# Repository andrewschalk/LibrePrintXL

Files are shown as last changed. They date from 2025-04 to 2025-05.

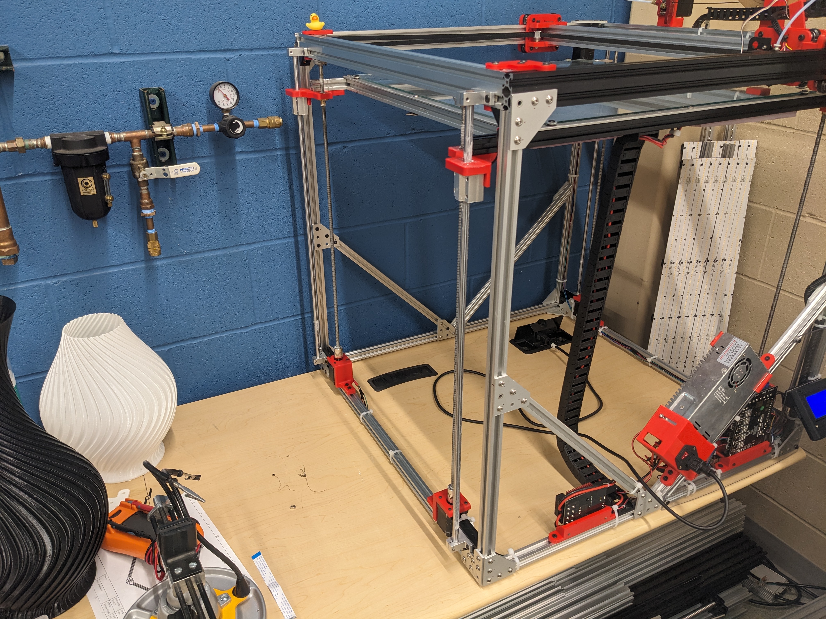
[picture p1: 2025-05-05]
Photos/Full_printer2.jpg

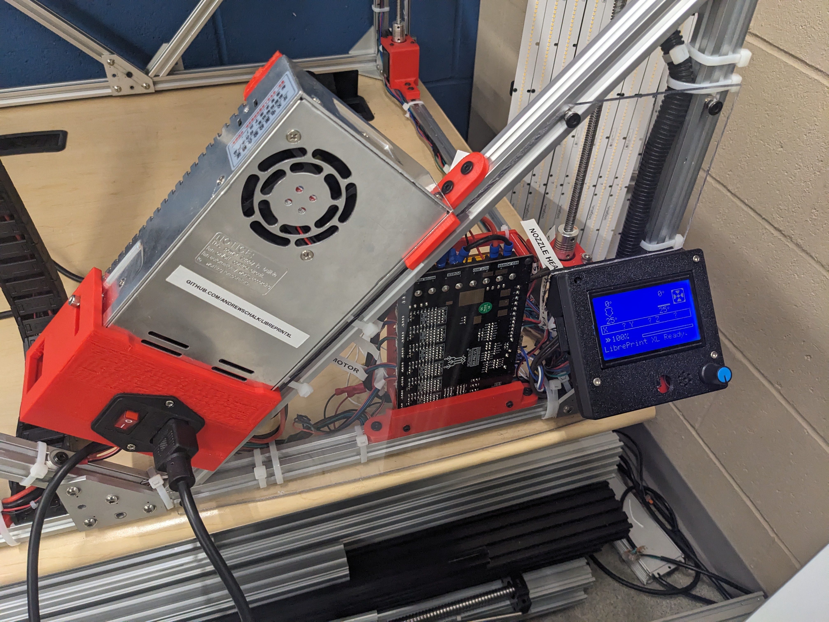
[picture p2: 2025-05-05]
Photos/Electronics_front2.jpg

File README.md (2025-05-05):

# LibrePrintXL
<p>

  </p>
A large open-source 3D printer.

See the [LibrePrint XL User Guide](/LibrePrint_XL_User_Guide.pdf) for steps on getting started.

See the v1.0.0 release on the right hand side for the full 3D model of the printer.







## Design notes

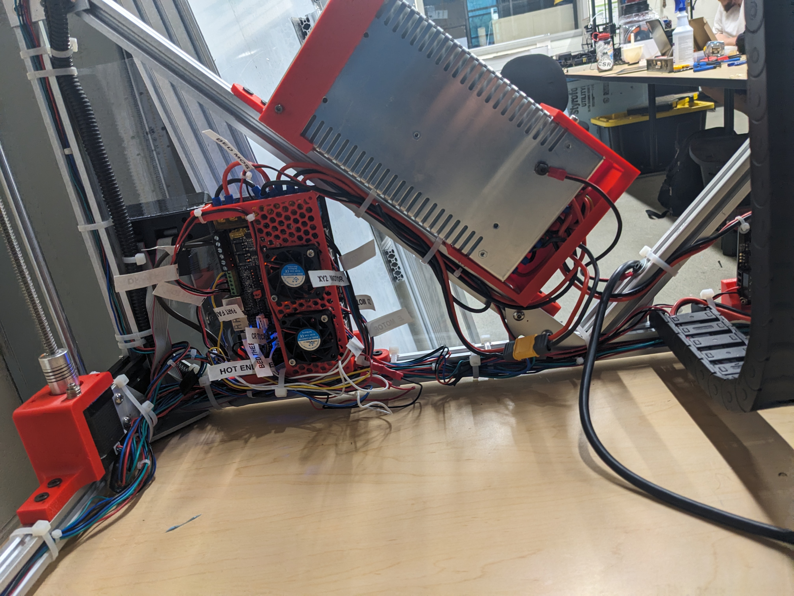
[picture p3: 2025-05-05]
Photos/Electronics_back.jpg

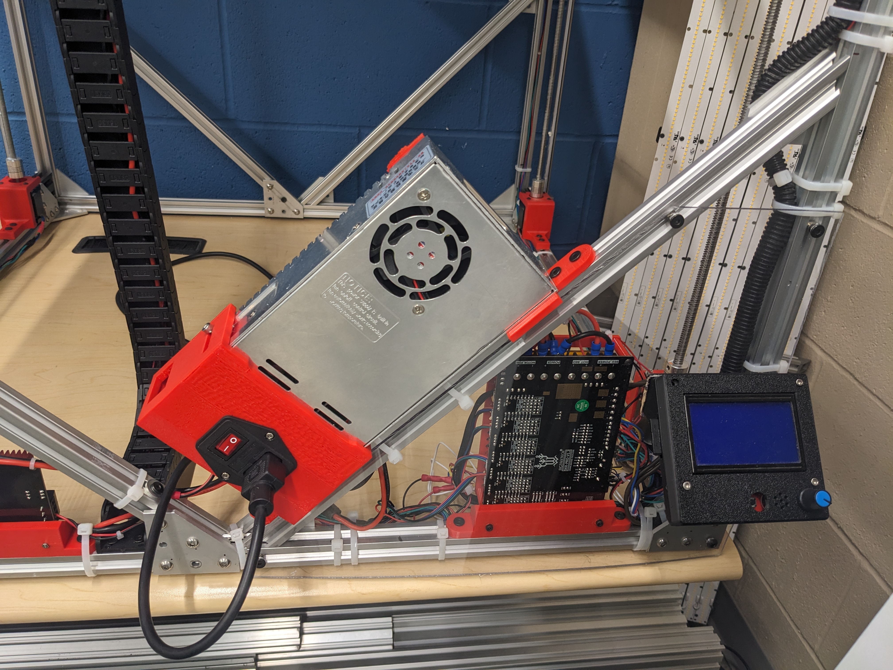
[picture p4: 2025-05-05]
Photos/Electronics_front.jpg

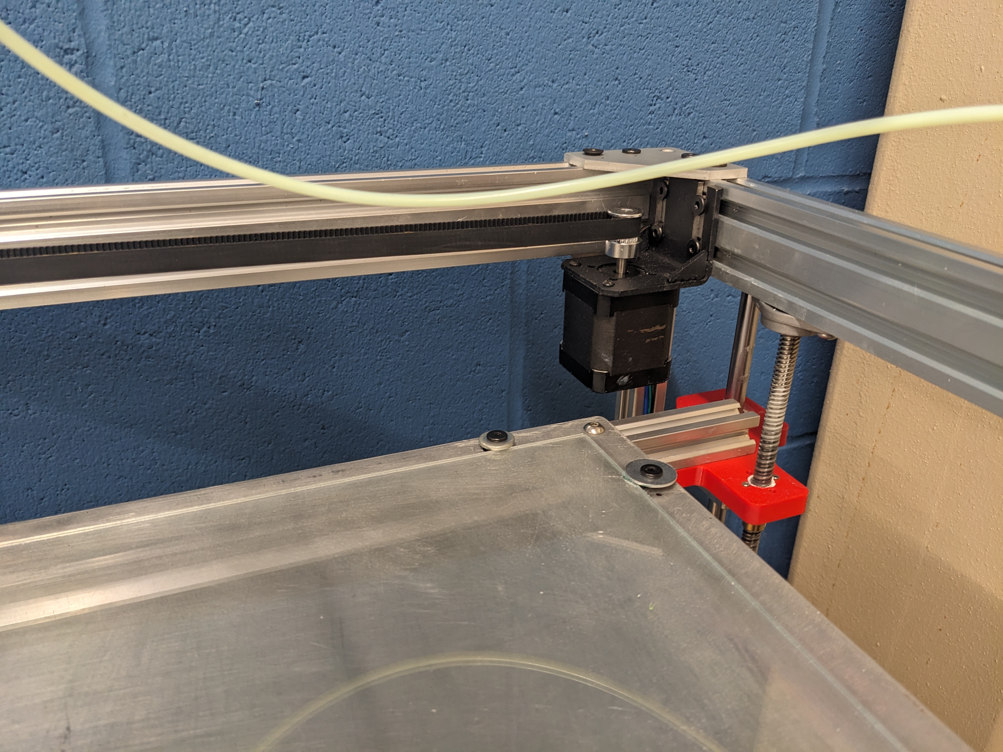
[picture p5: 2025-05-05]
Photos/CoreXY_Motor2.jpg

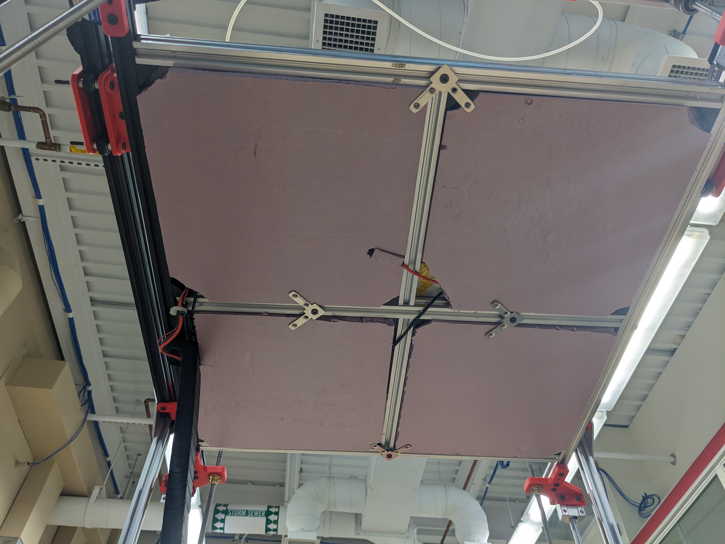
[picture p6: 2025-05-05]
Photos/Bed_underside.jpg

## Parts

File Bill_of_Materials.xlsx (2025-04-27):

Item | Part Number | Thumbnail | BOM Structure | Unit QTY | QTY | Stock Number | Description | REV
1 | HotBed |  | Normal | Each | 1
2 | 80-20610mm |  | Normal | Each | 2
3 | 80-20570mm |  | Normal | Each | 3
4 | 80-20275mm |  | Normal | Each | 2
5 | 4844N42_T-Slotted Framing Structural Bracket |  | Normal | Each | 10 |  | STEP AP203 | ANY
6 | HeatBed |  | Normal | Each | 4
11 | BLTouch-Smart V3.1 |  | Normal | Each | 0
13 | QSM-M5-4 |  | Normal | Each | 1 |  | SolidWorks IGES file using analytic representation for surfaces
15 | NF-A4x20 |  | Normal | Each | 2 |  | STEP AP214
16 | GantryPlate |  | Normal | Each | 6
17 | GantryBearing |  | Normal | Each | 12
18 | UNI 5931 - M 5 x 50 |  | Purchased | Each | 20 |  | Cylinder Head Cap Screw
20 | AS 1112 - M5 Type 5 |  | Purchased | Each | 20 |  | ISO metric hexagon nuts, including thin nuts, slotted nuts and castle nuts
23 | BeltFastener |  | Normal | Each | 2
24 | UNI 5931 - M 5 x 8 |  | Purchased | Each | 222 |  | Cylinder Head Cap Screw
25 | .25inSpacer |  | Normal | Each | 32
26 | 5mmSpacer |  | Normal | Each | 14
27 | 6627T231_Stepper Motor |  | Normal | Each | 7 |  | STEP AP203 | ANY
28 | 80-20base1 |  | Normal | Each | 2
29 | 80-20base2 |  | Normal | Each | 2
30 | 80-20Upright |  | Normal | Each | 4
31 | topBar1x2 |  | Normal | Each | 2
32 | topBar1x22 |  | Normal | Each | 2
33 | TSlotCornerGusset |  | Normal | Each | 10
34 | TSlotCornerGussetModified |  | Normal | Each | 4
35 | LinearRodSupport8020 |  | Normal | Each | 4
36 | CornerBracket |  | Normal | Each | 8
37 | 1277N11_Corrosion-Resistant Timing Belt Pulley |  | Normal | Each | 2 |  | STEP AP203 | ANY
38 | 1277N735_Corrosion-Resistant Timing Belt Pulley |  | Normal | Each | 8 |  | STEP AP203 | ANY
42 | 4516T501_Snap-Together Cable and Hose Carrier |  | Normal | Each | 34 |  | STEP AP203 | ANY
44 | SpoolHolder |  | Normal | Each | 0
45 | LinearRod |  | Normal | Each | 4
46 | Gantryconnect |  | Normal | Each | 4
47 | GantryBar |  | Normal | Each | 1
48 | Leadscrew nut M8 step2 by prodes |  | Normal | Each | 4 |  | STEP AP214 | ANY
49 | SC10 SCS10UU Linear Rail Bearing |  | Normal | Each | 4
50 | RodToBedCoupler |  | Normal | Each | 2
51 | 2391N25_Fast-Travel Ultra-Precision Lead Screw |  | Normal | Each | 4 |  | STEP AP203 | ANY
52 | RodToBedCouplerMirror |  | Normal | Each | 2
53 | Zinc Alloy Pillow Block Flange Bearing KFL08 ID-8mm |  | Normal | Each | 4
54 | UNI 5931 - M 3 x 5 |  | Purchased | Each | 48 |  | Cylinder Head Cap Screw
55 | NEMA17BaseHolder |  | Normal | Each | 4
56 | SK10 |  | Normal | Each | 8
57 | AS 1421 - M5 x 12 Cup Point |  | Purchased | Each | 8 |  | ISO metric hexagon socket set screws
58 | nema17-mount |  | Normal | Each | 2 |  | FreeCAD Model
59 | CoreXYPullyBlock |  | Normal | Each | 4
60 | RepRapDiscount_Full Graphic Smart Controller |  | Normal | Each | 1
61 | FG_lcd_front_Panel |  | Normal | Each | 1
62 | FG_lcd_rear_cover |  | Normal | Each | 1
63 | FAN |  | Normal | Each | 1
64 | SKR-PRO-V1.2 |  | Normal | Each | 1
65 | SKR Mount |  | Normal | Each | 1
66 | UNI 5931 - M 5 x 20 |  | Purchased | Each | 4 |  | Cylinder Head Cap Screw
67 | TMC2209 |  | Normal | Each | 6 |  | FreeCAD Model
68 | Raspberry Pi 4 Model B |  | Normal | Each | 1
69 | Raspberry_Pi_4_Case |  | Normal | Each | 1 |  | STEP AP214 | ANY
70 | UNI 5931 - M 2.5 x 4 |  | Purchased | Each | 4 |  | Cylinder Head Cap Screw
71 | Power Supply Cover Assembly |  | Normal | Each | 1
74 | 4147N168_Set Screw Precision Flexible Shaft Couplings |  | Normal | Each | 4 |  | STEP AP203 | ANY
75 | 10mmSpacer |  | Normal | Each | 8
76 | makerbase mks hotbed mos v1.1 |  | Normal | Each | 1 |  | CATIA V5 STEP Exchange
77 | HOTBED-MOSHolder |  | Normal | Each | 1
80 | Part2 | *Varies* | Normal | Each | 2
81 | Part1 | *Varies* | Normal | Each | 2
82 | Idler Bearing |  | Normal | Each | 1
83 | MK8 Drive Gear |  | Normal | Each | 1
84 | MK8_Exruder_004(yay) |  | Normal | Each | 1
85 | Part3 |  | Normal | Each | 1
86 | extruder motor stand |  | Normal | Each | 1
87 | FrameCrossBrace |  | Normal | Each | 4
88 | 45CornerGusset |  | Normal | Each | 8
89 | HOTEND ENDER 3 PRO |  | Normal | Each | 1
90 | DUTO DE AR BLOWER FAN DC PB04020MS4 |  | Normal | Each | 1
91 | BLOWER FAN DC PB04020MS4 |  | Normal | Each | 1
92 | Vis BHC 18mm |  | Normal | Each | 3
93 | CableCarrierMount |  | Normal | Each | 1
94 | UNI 5931 - M 5 x 25 |  | Purchased | Each | 1 |  | Cylinder Head Cap Screw

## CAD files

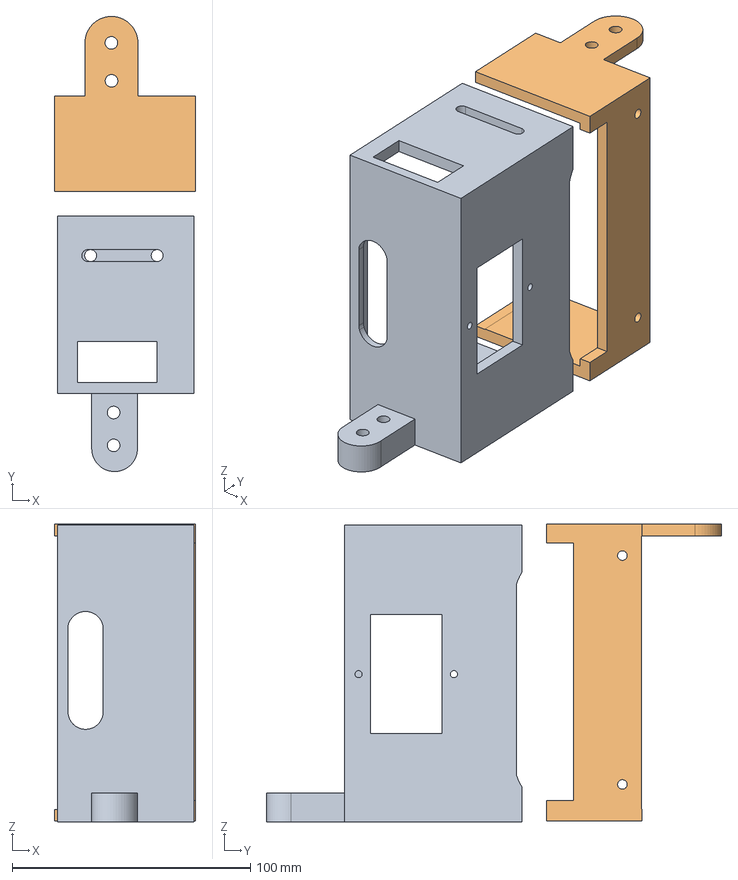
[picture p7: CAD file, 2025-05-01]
3D_Models/Power-supply-connector.stp
59.3 x 191.0 x 125.0 mm

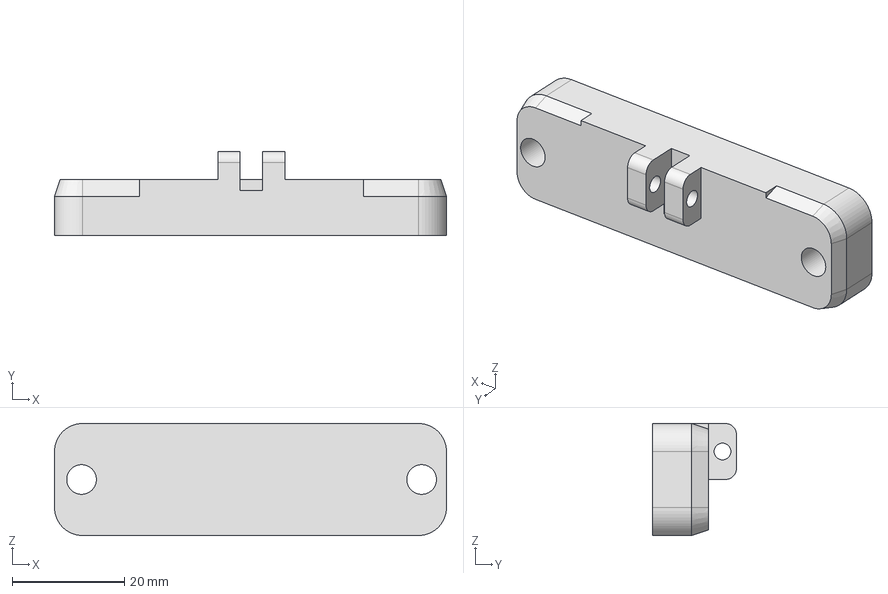
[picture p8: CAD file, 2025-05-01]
3D_Models/cameramountbottom.stp
70.0 x 15.0 x 20.0 mm

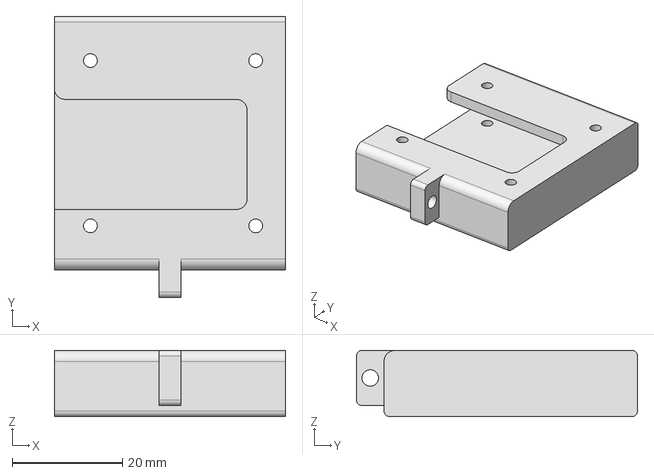
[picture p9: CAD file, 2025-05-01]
3D_Models/cameramounttop.stp
42.0 x 51.0 x 12.0 mm

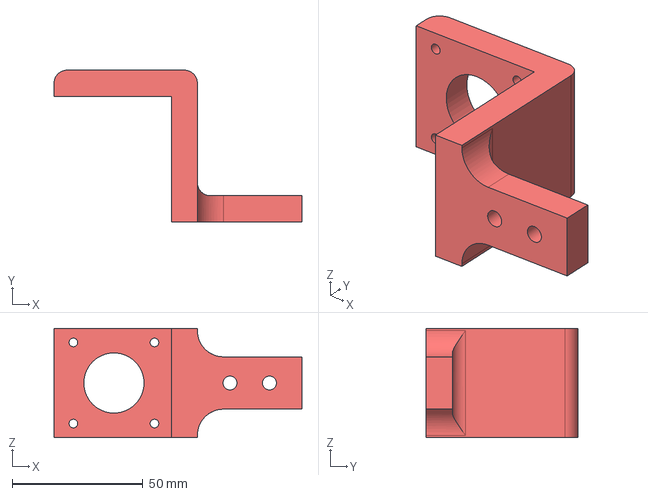
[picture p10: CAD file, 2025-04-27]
3D_Models/NEMA17BaseHolder.stp
94.8 x 58.0 x 41.8 mm

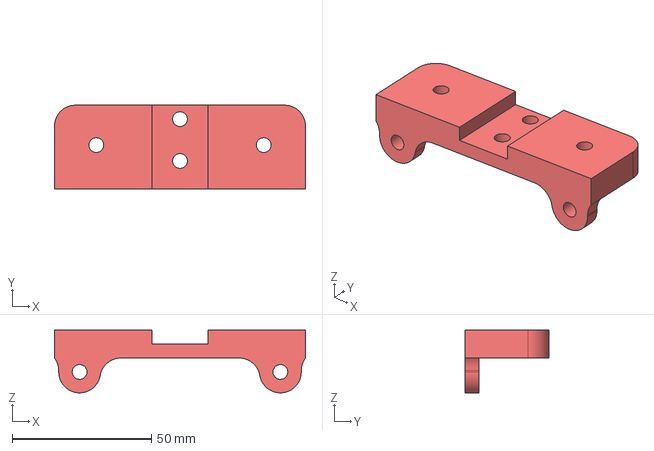
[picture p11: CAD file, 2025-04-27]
3D_Models/Gantryconnect.stp
90.0 x 30.0 x 22.5 mm

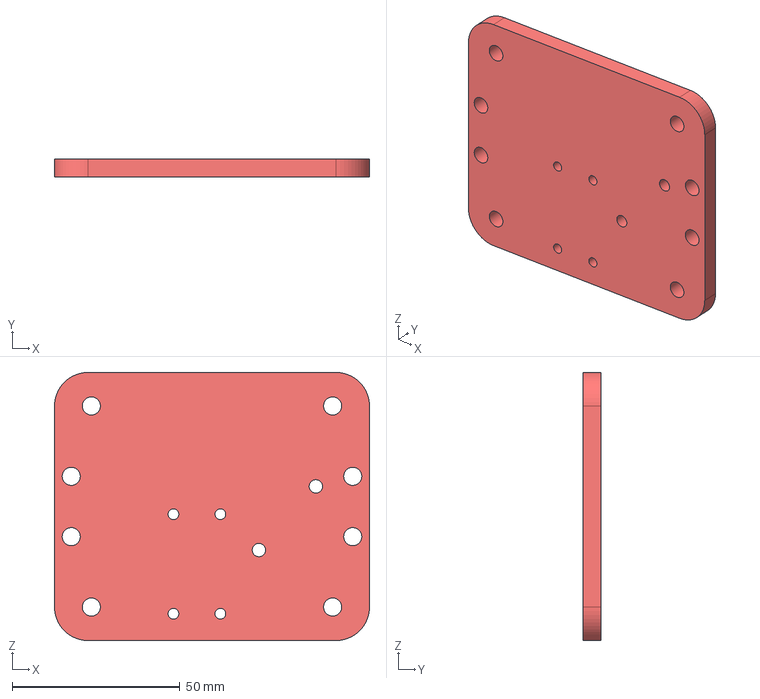
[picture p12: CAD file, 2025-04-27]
3D_Models/GantryPlate.stp
94.0 x 5.50 x 80.0 mm

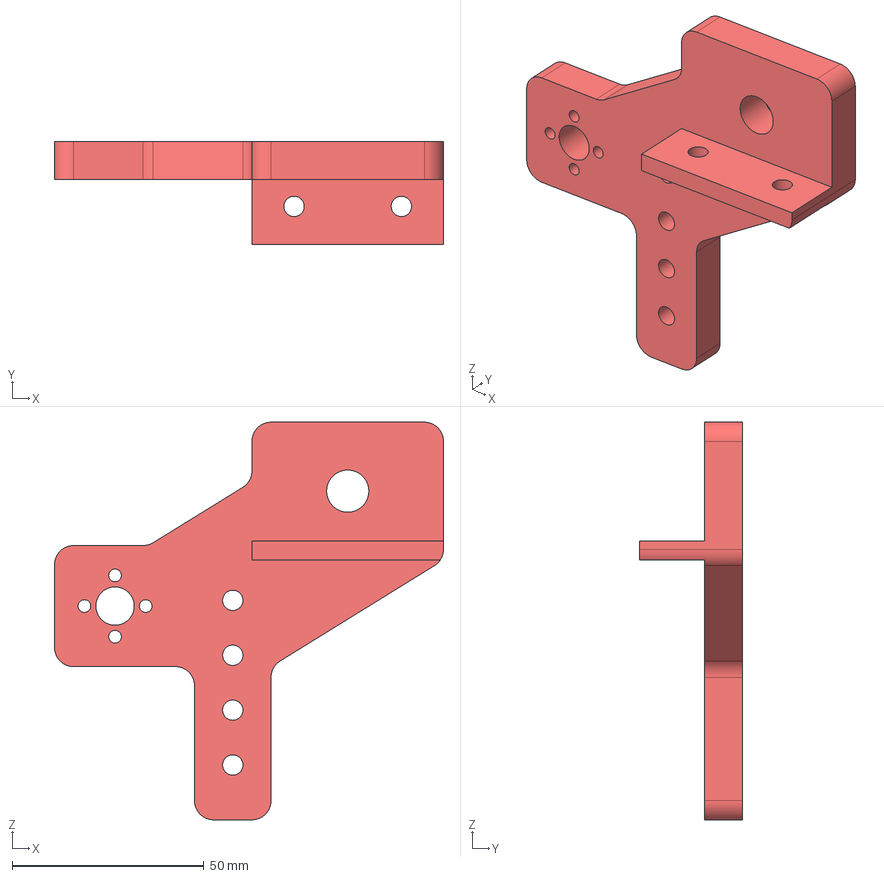
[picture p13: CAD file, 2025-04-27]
3D_Models/RodToBedCoupler.stp
101.5 x 27.0 x 103.8 mm

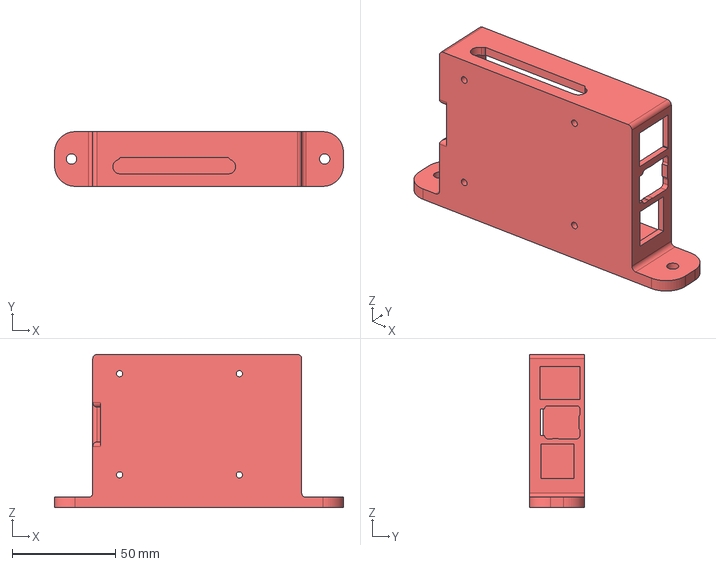
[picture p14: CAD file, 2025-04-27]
3D_Models/Raspberry_Pi_4_Case.stp
140.0 x 26.5 x 74.1 mm

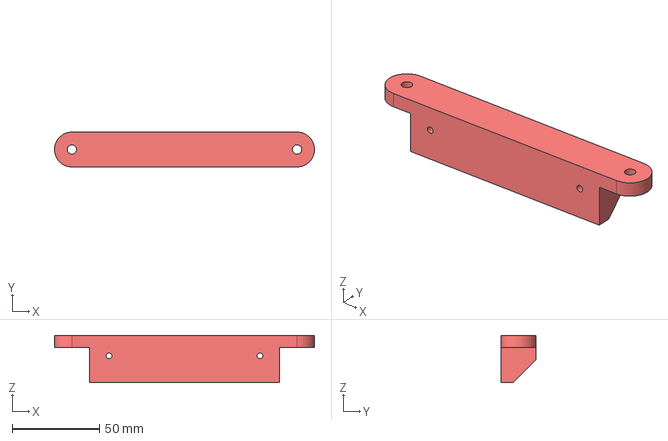
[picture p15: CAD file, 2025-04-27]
3D_Models/SKR Mount.stp
149.0 x 20.0 x 27.0 mm

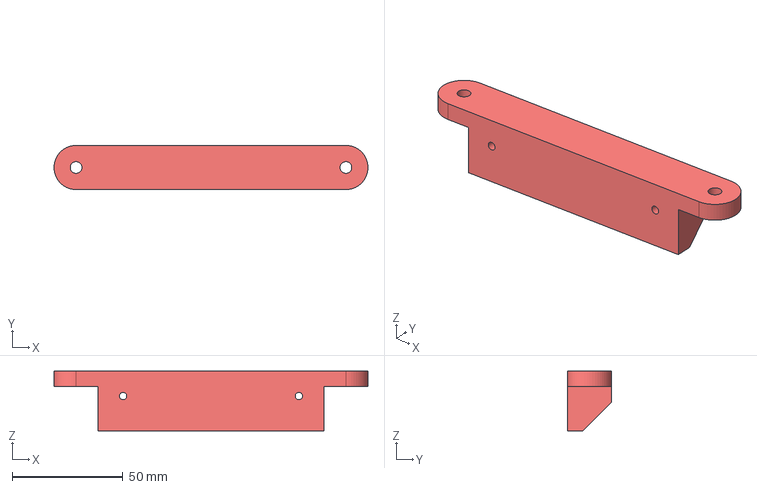
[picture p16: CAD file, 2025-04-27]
3D_Models/HOTBED-MOSHolder.stp
142.0 x 20.0 x 27.0 mm

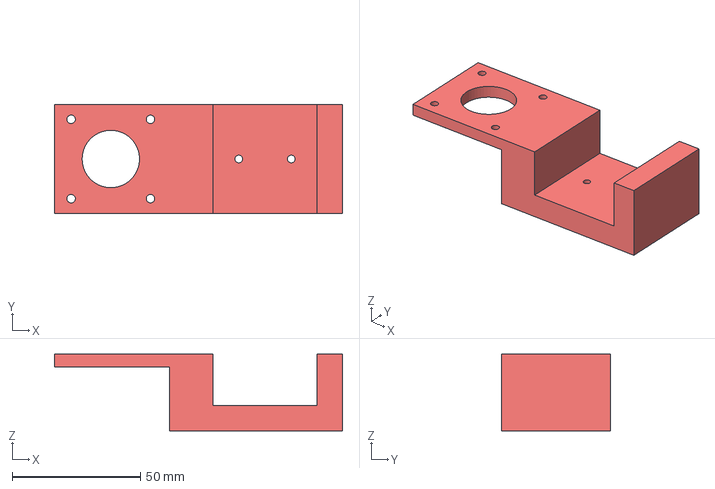
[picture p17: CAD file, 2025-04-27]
3D_Models/extruder motor stand.stp
112.5 x 42.5 x 30.0 mm

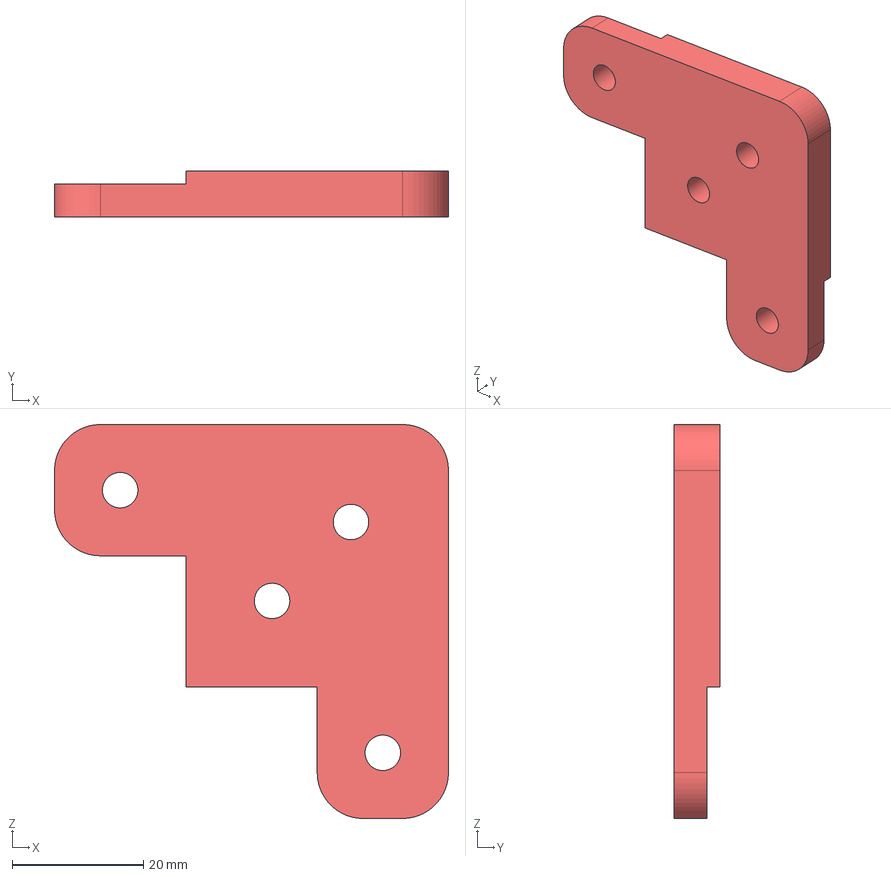
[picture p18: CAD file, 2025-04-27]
3D_Models/CoreXYPullyBlock.stp
60.0 x 7.00 x 60.0 mm

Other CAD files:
3D_Models/FG_lcd_front_Panel.stp
3D_Models/RodToBedCouplerMirror.stp
3D_Models/FG_lcd_rear_cover.stp
3D_Models/FANCover.stp

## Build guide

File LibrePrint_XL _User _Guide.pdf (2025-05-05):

# LibrePrint XL

## User Guide and Manual

## Created by

## Andrew Schalk

## Liam McGuire

## Reno Hoffman

## Christobol Alvarado

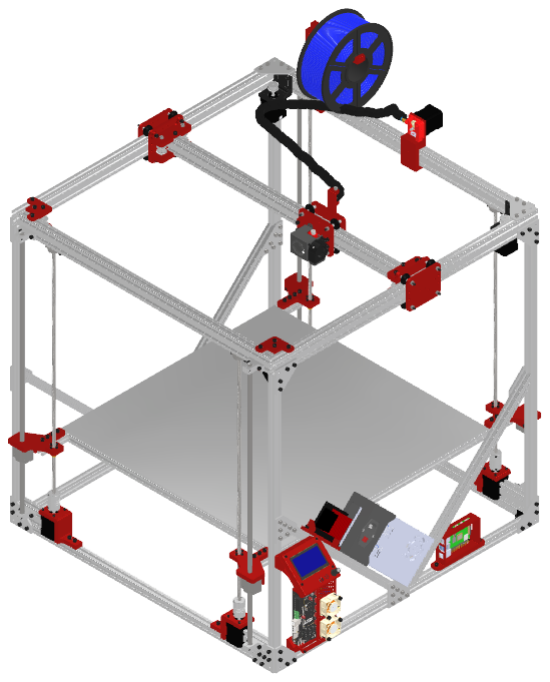
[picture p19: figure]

## Contents

## Printing a Part

Setting up PrusaSlicer

- Download and install the latest version of PrusaSlicer. (https://www.prusa3d.com/page/prusaslicer_424/) At the time of writing, this is
2.9.2. Any 2.X.X version of PrusaSlicer will be compatible with LibrePrint XL.
- Download “PrusaSlicer_LibrePrintXL.ini” from the Github (https://github.com/andrewschalk/LibrePrintXL). Be warned that using other profiles can lead to failed prints and even printer damage.
- Navigate to File -> Import -> Import Config Bundle. In the file browser that opens, select the profile you downloaded from Github.
- LibrePrint XL’s profiles are now loaded and you are ready to slice a model!

Slicing a Model

- The usage of PrusaSlicer is documented extensively on their website. (https://help.prusa3d.com/article/general-info_1910)
- Ensure that the proper profiles are selected
- Under “Print Settings” select “LibrePrintXL”
- Under “Filaments” select “LibrePrintXL_PLA”
- Under “Printers” select “LibrePrintXL”
- No modifications to these profiles are needed
- Add a model to the print space, slice the model, and export the Gcode to an SD card.

Mechanical Calibration

- Visually inspect the bed, if it looks to be out of level by greater than 2° in any direction, manual leveling must be performed (see “manual bed leveling). Software bed leveling will account for small errors in bed levelness, but large errors can cause mechanical failure.
- Make sure that the printer has enough room for moving parts to not contact surrounding objects. Ensure that:
- All four corners of the bed can move up and down
- The wire carrier which holds the wires for the print head can protrude horizontally above the user interface
- The y-gantry on both sides can move forwards and backwards.

- The space beneath the printer is clear

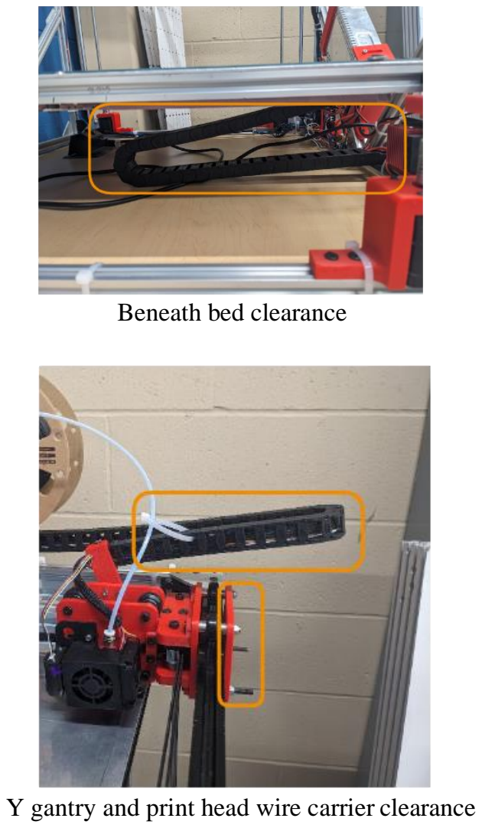
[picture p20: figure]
Beneath bed clearance

Y gantry and print head wire carrier clearance

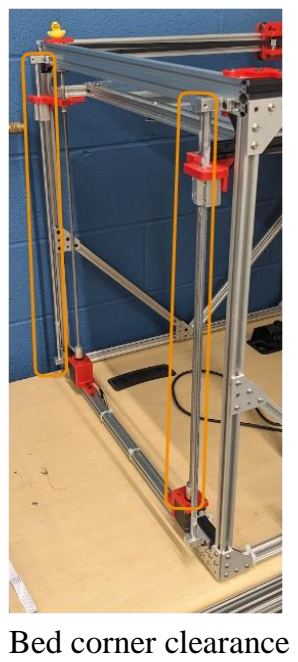
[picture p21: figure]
Bed corner clearance

Printing a File

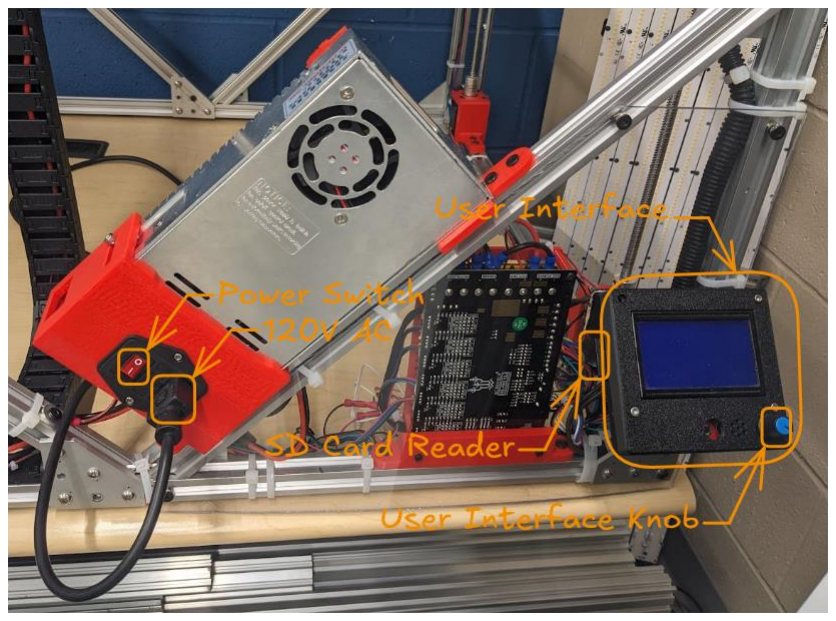
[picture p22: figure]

- See “Unloading Filament” and “Loading Filament” if filament needs to be replaced
- Put the SD card in the slot on the left side of the user interface.
- Turn on the printer with the power switch
- Wait for the info screen to appear
- Press the knob on the user interface to enter the menu. Turning the knob will navigate through the menu
- Select Print from Media -> YourFileName.gcode -> Print
- The info screen will appear saying “Bed Heating…” at the bottom, indicating that the print is starting.
- The bed and hot end will heat up, all three axes will move to home, and the print head will probe the bed. Once this is complete, the printing will begin.
- Verify that the first layer is printed properly and allow the print to complete
- The screen will indicate the percentage completed and how long the print has been running.

Unloading Filament (For PLA)

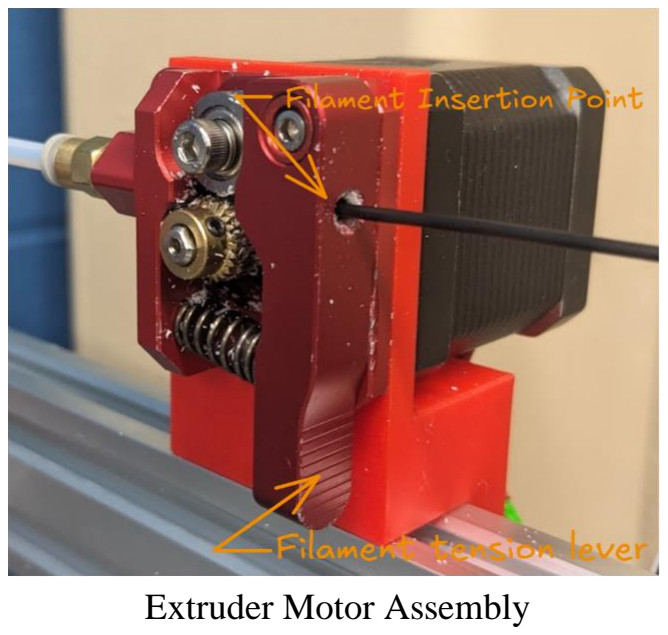
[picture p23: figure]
Extruder Motor Assembly

- Heat up the extruder nozzle to 260°C using the user interface.
- Press the user knob to navigate to the main menu.
- Select Temperature -> Nozzle
- Turn the knob until the number reads 260°C
- Press the knob. The nozzle will begin to heat up and you will be taken back to the temperature page.
- Select Main -> Info Screen to monitor the temperature
- Once the nozzle has reached 260°C, you may begin unloading filament
- Press and hold the filament tension lever to free the filament
- Pull the filament gently until it comes completely out of the printer
- If the filament is hard to pull, first push the filament farther into the extruder to melt built up plastic off of the end and then pull

Loading Filament (For PLA)

- From the “Unloading Filament” section, the nozzle should already be heated to 260°C. If not, the following steps describe the heating process
- Press the user knob to navigate to the main menu.
- Select Temperature -> Nozzle
- Turn the knob until the number reads 260°C
- Press the knob. The nozzle will begin to heat up and you will be taken back to the temperature page.
- Select Main -> Info Screen to monitor the temperature
- Once the nozzle has reached 260°C, you may begin loading filament.

- Cut off any ragged bits at the end of the filament and straighten out the last 2 inches by hand
- Press and hold the filament tension lever
- Insert the filament into the filament insertion point and push the filament until it begins to extrude out of the nozzle
- Wait until the old color has been purged, the filament has been successfully loaded and you are ready to print
- Remove any stray plastic that may have been extruded during filament loading

## Troubleshooting

LibrePrint XL is based on standard 3D printer design methods so the solutions to any issues not listed here can usually be found online.

First layer issues

- The nozzle is too close or too far from the bed
- During a print, the z-offset may be set by menu -> tune -> Z babystepping
- While the first layer is being laid by the printer, turn the knob to slowly move the nozzle away or towards the bed

CoreXY belt loose

- If the belt comes loose, pull belt taught and tighten screws on the extruder mount holding belt in place. The belt should be tight enough to be easy to move and vibrate like a guitar string when plucked but not loose enough to sag.
- Command the X axis and Y axis to move using the touch screen, observe their movements to ensure they move properly. Info Screen -> Main Screen -> Move Axis -> Move X -> 1mm.
- Move in the X-axis several times to ensure it moves correctly
- Repeat the process for the Y-Axis
- Info Screen -> Main Screen -> Move Axis -> Move Y -> 1mm.

Thermal Runaway

- The screen displays “THERMAL RUNAWAY PRINTER HALTED Please reset”
- This is the printer recognizing an issue with the commanded heating and the sensed temperature.
- Test the operation of the heating functions !!While it is not likely, it is possible that these systems could heat to a dangerous level if broken, keep an eye on the heat while troubleshooting
- Heat the nozzle to 260°C

- Heat the bed to 60°C
- If both systems work well, the system is likely fine, this error may have been a false positive. If the error occurs again, check the thermal sensor and heating element for loose wiring.
- If one system fails, note the actual temperature and displayed temperature
- If the system begins to heat but the temperature doesn’t change, consider rewiring or replacing the temperature sensor
- If the system does not heat, consider rewiring or replacing the heating element

Filament Slipping

- If there is an issue with any part of the extruder assembly, it may cause the filament to slip preventing it from printing properly
- Brass pinion gear on extruder motor shaft may not be contacting filament
- If the brass pinion gear is not contacting the filament unscrew the set screw in the pinion, move the pinionup towards the filament and then tighten it back on
- To test extrusion, begin by heating the extruder to 260°C this can be done by menu ->temperature -> nozzle
- Once the nozzle is heated up, feed the filament into the extruder.
- Menu -> Motion -> Move Axis -> Move Extruder -> Move 1mm.
- Rotate the user knob until the filament extrudes from the nozzle.
- Observe extruder motor and ensure gear is moving filament.

Under Extrusion

- Ensure that the filament roll is oriented on the stand such that the plastic is being fed into the extruder at the same height.
- Measure on the filament role from the entrance of the extruder motor to a pre-determined distance. 10-20mm should be sufficient. Mark the filament that distance
- Rotate the user knob that distance. The mark should reach the entrance of the extruder motor and stop.

Hot-End Loose

- !! This may be a symptom of other issues. If the hot end fan is not working, the hot end fasteners may get too hot causing the hot end to sag in the plastic.
- The hot end fan will turn on if the hot end is above 60°C.
- Verify that the fan turns on by setting the hot end temperature to 260°C and waiting for the fan to turn on. menu -> temperature -> nozzle
- This may be fixed by retightening the two bolts that hold the hot end to its mount. These are held tight with lock washers so there should be no need for thread locker. If they keep coming loose, add thread locker.
- The two screws may be reached by putting through

Z-axis Squeaking or Binding

- Review procedure for manual bed leveling
- Review procedure for lubricating z-axis
- Verify all z-axis fasteners are tight by attempting to wiggle the parts they fasten

Loose Parts/Fasteners

The fasteners are all held in place by either thread locker or nylon lock nuts. When tightening fasteners, be considerate of the materials being held together and the force used. Plastic and even aluminum can deform from tightening too much.

- If a nylon lock nut becomes loose, it may be sufficient to tighten it back into place. If it does not stay in place, replace the lock nut with a new one.
- If there is not a nylon lock nut, the fastener is held in place with thread locker. The fastener must be removed and thread locker(locktite blue is good, do not use red) applied before retightening.

Broken Part

- Any part may be found in the bill of materials for replacement
- 3D printed part files are in the LibrePrint XL GitHub
- When replacing fasteners, they need to be properly secured again. If this is not done, the part may become loose, causing print failures or printer damage.
- Fasteners with nylon lock nuts should have the lock nut replaced, lock nuts lose some of their locking force after being used once.
- Fasteners without nylon lock nuts should have thread locker (locktite blue is good, do not use red) applied before securing.

Stringy and Saggy print(or other print quality issues)

This can be caused by many issues so it may be best to search up the specific issue online. This kind of error can usually be fixed by tuning slicer settings.

- Different brands of filament may need different settings even if they’re the same type of plastic.
- The temperature that we found worked best for the overture brand filament was 260°C. Another (no-name brand) was found to work best around 220°C and 260°C was far too hot. Research a “temperature tower” to tune the temperature for your filament.

## Electrical Specifications

- The frame and bed are connected to earth through the power supply case.

Wiring Schematic

- Each wire is labeled with a white flag to identify what it is
- Example: “XY1” means that this is the XY1 motor
- Use the following schematic to find the ports that these devices plug into
- Wire pairs which consist of just a red and black wire will plug into the positive and negative pins respectively
- Most connectors can only be plugged in one way. The exception is the CR touch whose connection is described in the schematic

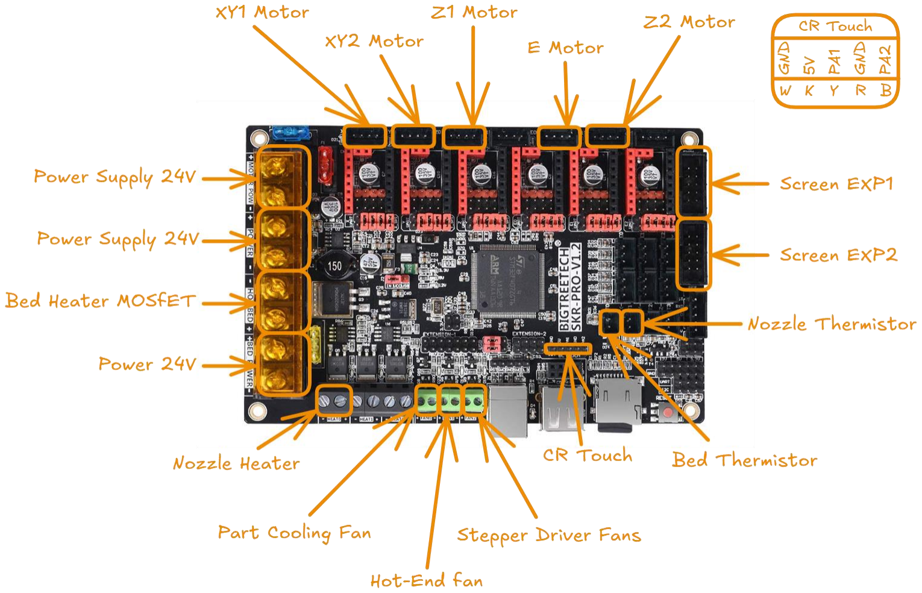
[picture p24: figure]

Bed Circuit Diagram

The 24V source is provided by the bed heater MOSFET

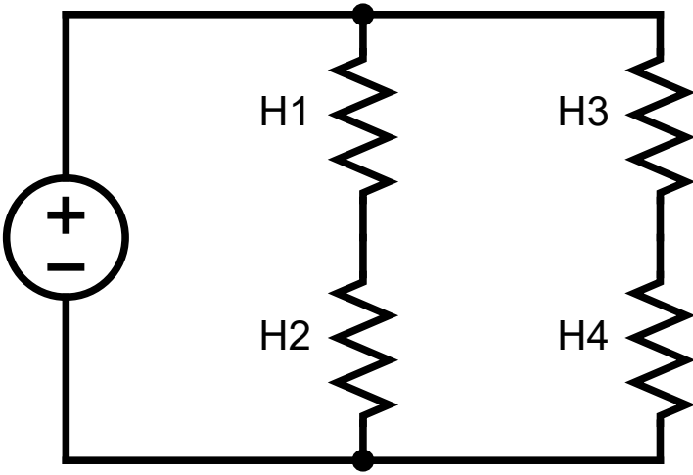
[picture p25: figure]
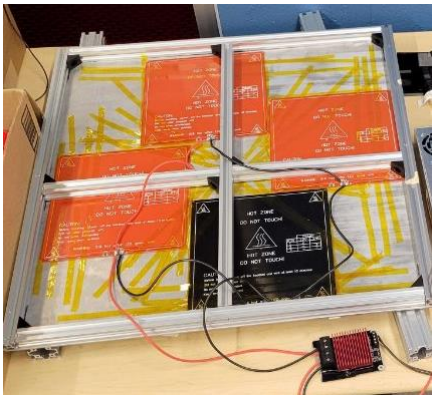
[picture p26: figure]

## Mechanical Specifications

CoreXY

## Firmware

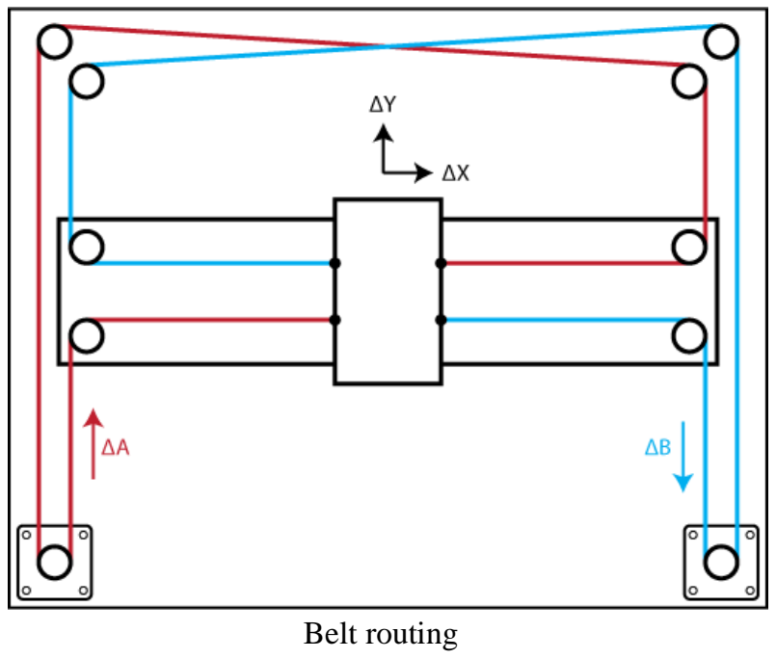
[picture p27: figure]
Belt routing

- LibrePrint XL uses a custom version of Marlin 2.1.2.5. Anything not discussed here can be referenced in the Marlin documentation. (https://marlinfw.org/)
- The files needed to rebuild LibrePrint XL’s firmware are on the GitHub. Marlin provides tutorials on how to develop and flash this firmware.

## Maintenance and Calibration

Manual Bed Leveling

This should be performed every 50 hours of printing or whenever the bed is out of level by greater than 2° in any direction. Software bed leveling will account for small errors in levelness, but large errors can cause mechanical failure.

- Needed
- A small, flat, object about ½ inch in one dimension. This will be used as a ground truth for the distance between the nozzle and points on the bed.

- Turn on the printer, press the user button, and select Motion -> Auto home. This will cause the printer to move to the home position
- Once homing is complete, from the motion menu, select Move Axis -> Move Z -> Move 1mm.
- Turn the knob clockwise to move the z-axis by 1mm increments until your flat object fits between the bed and the nozzle. This does not need to be precise
- Turn off the printer. (This disables the motors for the next step)
- Each corner of the bed will be brought to the same height by moving the nozzle to each corner and adjusting the position of the motor at that corner
- With your flat object between the nozzle and bed, rotate the coupling at the base of the z-axis lead screw to move the bed up until the nozzle just barely contacts the top of your flat object. The best way to do this is to move your flat object back and forth slowly on the bed while moving the bed up. You’ll know when the nozzle is touching when you feel a small amount of resistance to moving your flat object.

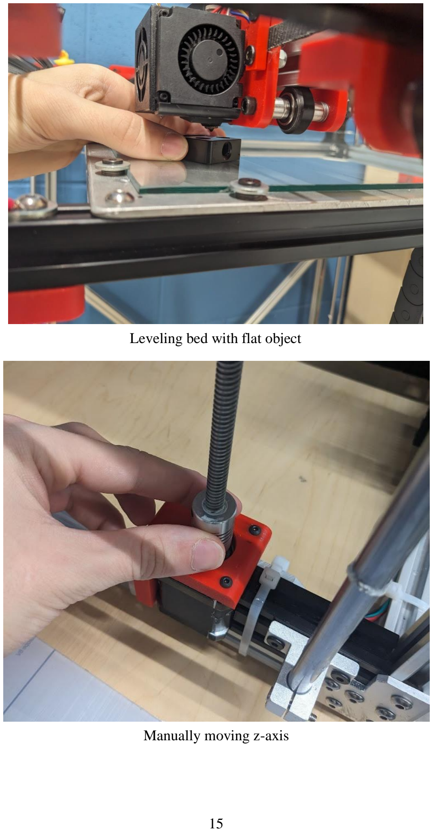
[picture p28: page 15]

Manually moving z-axis

Leveling bed with flat object

- By hand, slowly move the print head close to another corner on the bed and repeat the prior step for each corner. !! Moving too fast will generate a voltage which could damage the printer, if the screen lights up while the printer is off, you’re moving too fast.
- After all corners have been set to the same height, bed leveling is complete.

Lubricating Z-axis

This should be performed every 100 hours of printing or whenever the z-axis starts to squeak.

- Needed
- White lithium grease (Lucas Oil Products Inc. NLGI #2 is what we used)
- All four z-axis lead screws and all four z-axis linear rods should be greased
- Squeeze a thin layer of grease (about 1/16 of an inch thick) onto the lead screws and linear rods, all the way from the top to the bottom.
- Use nitrile gloves or a paper towel to spread the grease all around the linear rods. This does not need to be done on the lead screws, the lead screws will spread the grease when they rotate.
- Move the z-axis through its entire range of motion by pressing the knob and selecting Motion -> Move Axis -> Move Z -> Move 10mm. Turning the knob will move the bed in 10mm increments
- Wipe off any excess grease built up from movement

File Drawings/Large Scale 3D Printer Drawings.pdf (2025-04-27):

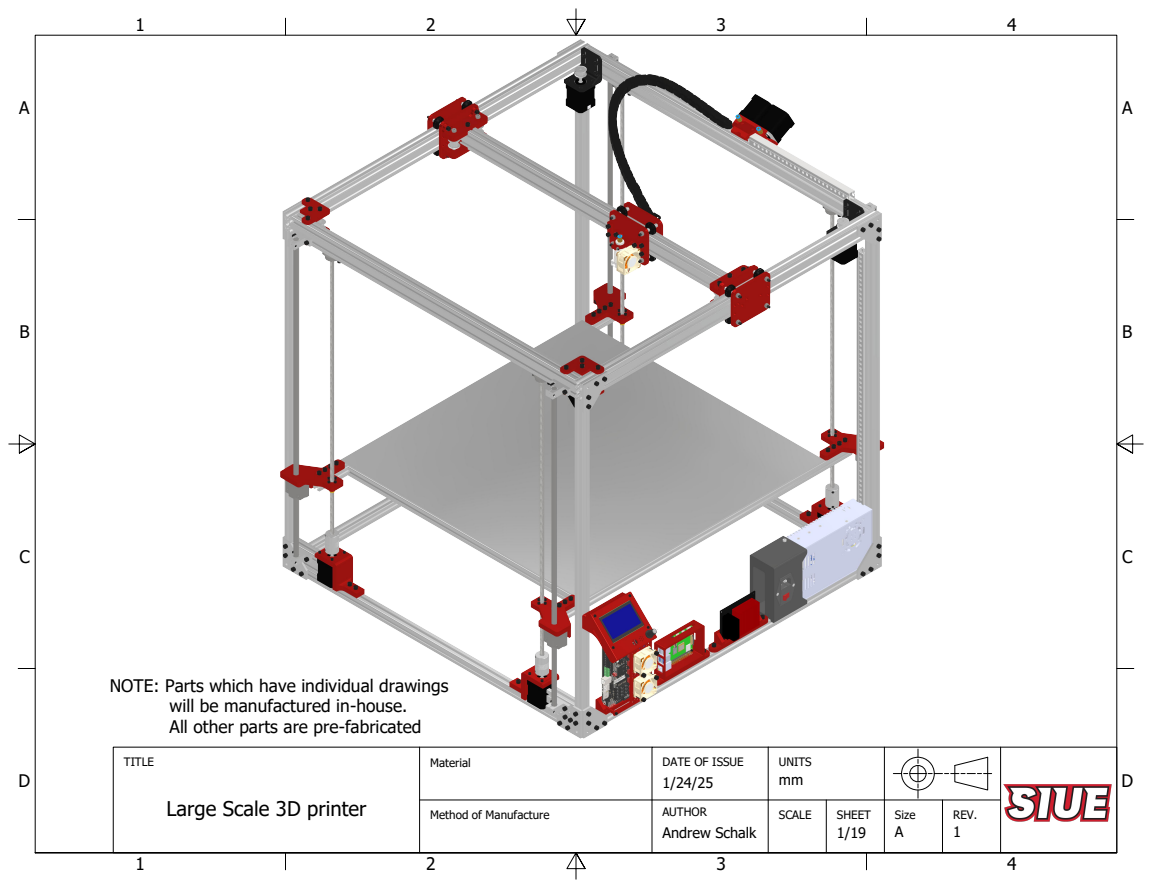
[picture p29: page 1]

NOTE: Parts which have individual drawings

will be manufactured in-house.
All other parts are pre-fabricated

TITLE Large Scale 3D printer | Material | DATE OF ISSUE 1/24/25 | UNITS mm

Method of Manufacture | AUTHOR Andrew Schalk | SCALE | SHEET | Size A | REV.

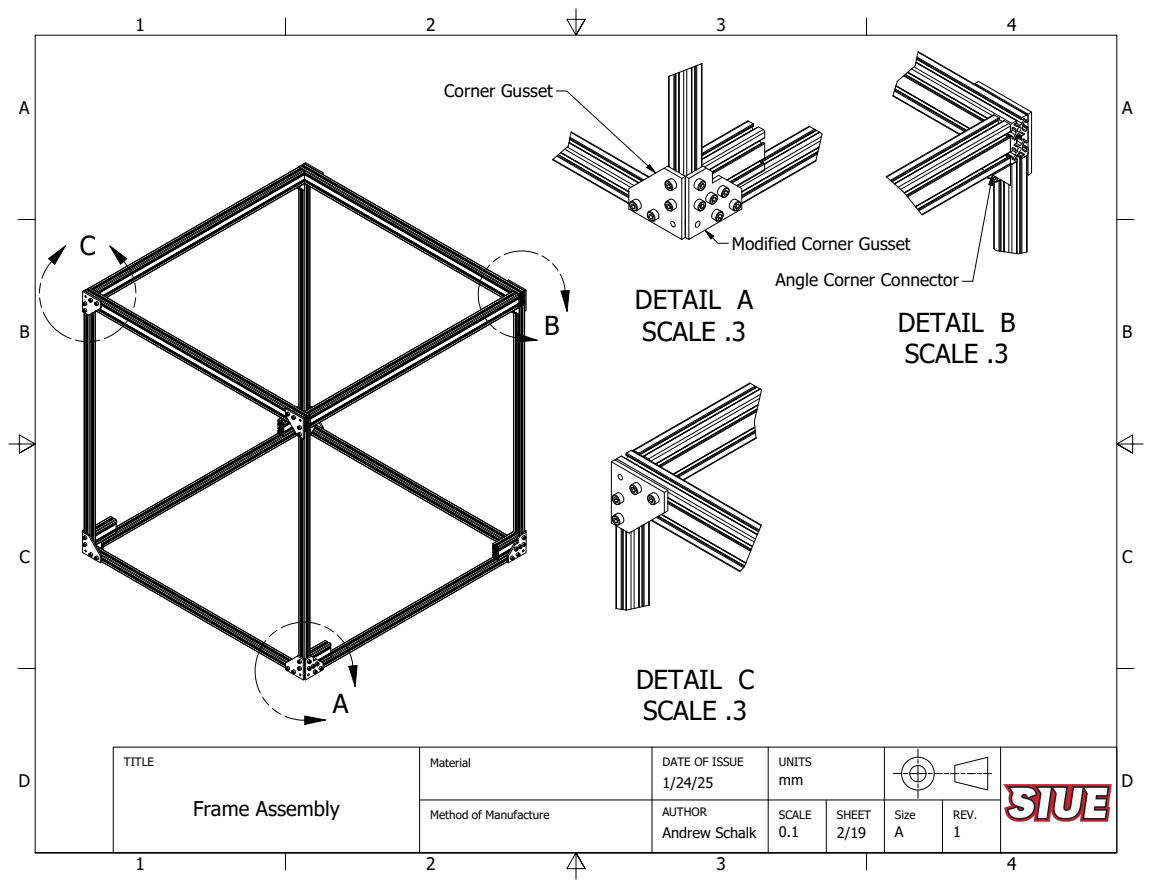
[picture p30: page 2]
DETAIL A; SCALE .3; DETAIL B; DETAIL C; Corner Gusset

Modified Corner Gusset

Angle Corner Connector

TITLE Frame Assembly | Material | DATE OF ISSUE 1/24/25 | UNITS mm

Method of Manufacture | AUTHOR | SCALE 0.1 | SHEET | Size | REV.

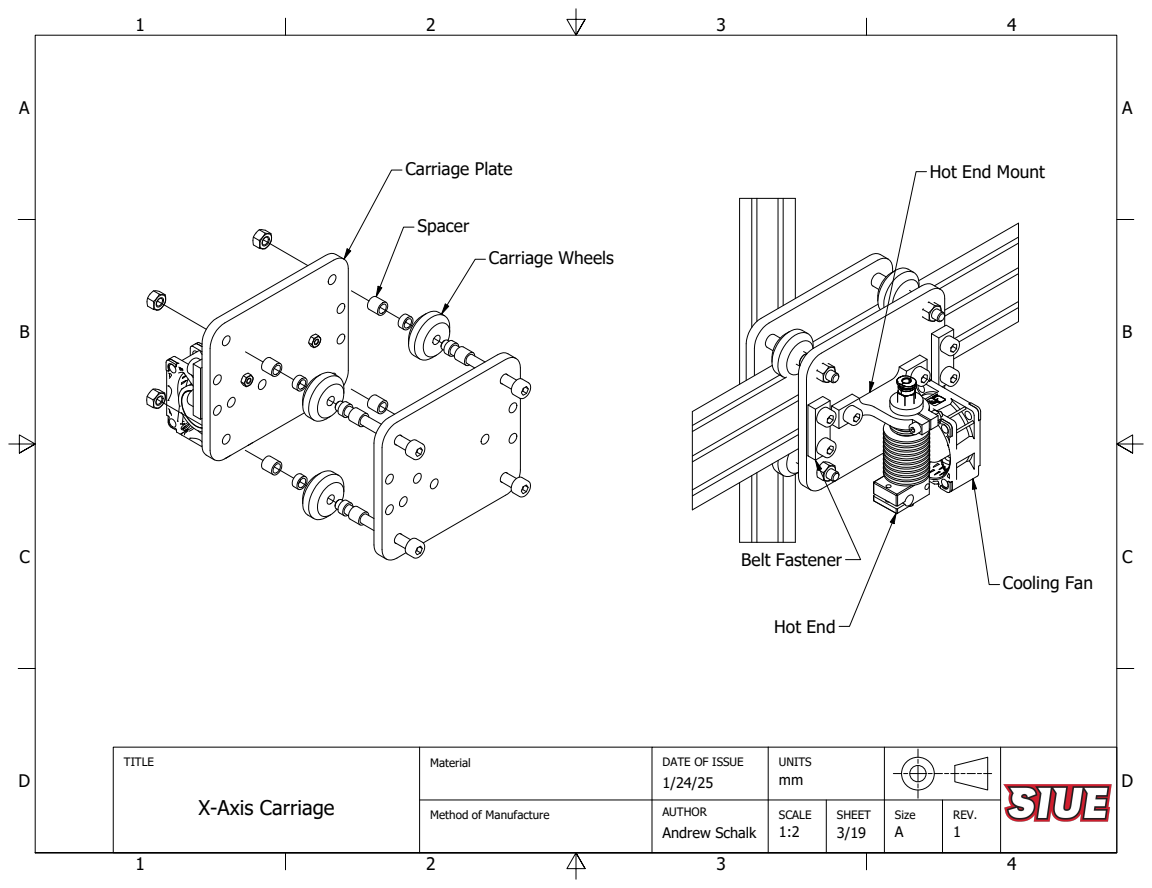
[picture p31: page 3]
Carriage Plate; Cooling Fan; Belt Fastener; Hot End; Carriage Wheels

Hot End Mount

TITLE X-Axis Carriage | Material | DATE OF ISSUE 1/24/25 | UNITS mm

Method of Manufacture | AUTHOR | SCALE 1:2 | SHEET | Size | REV.

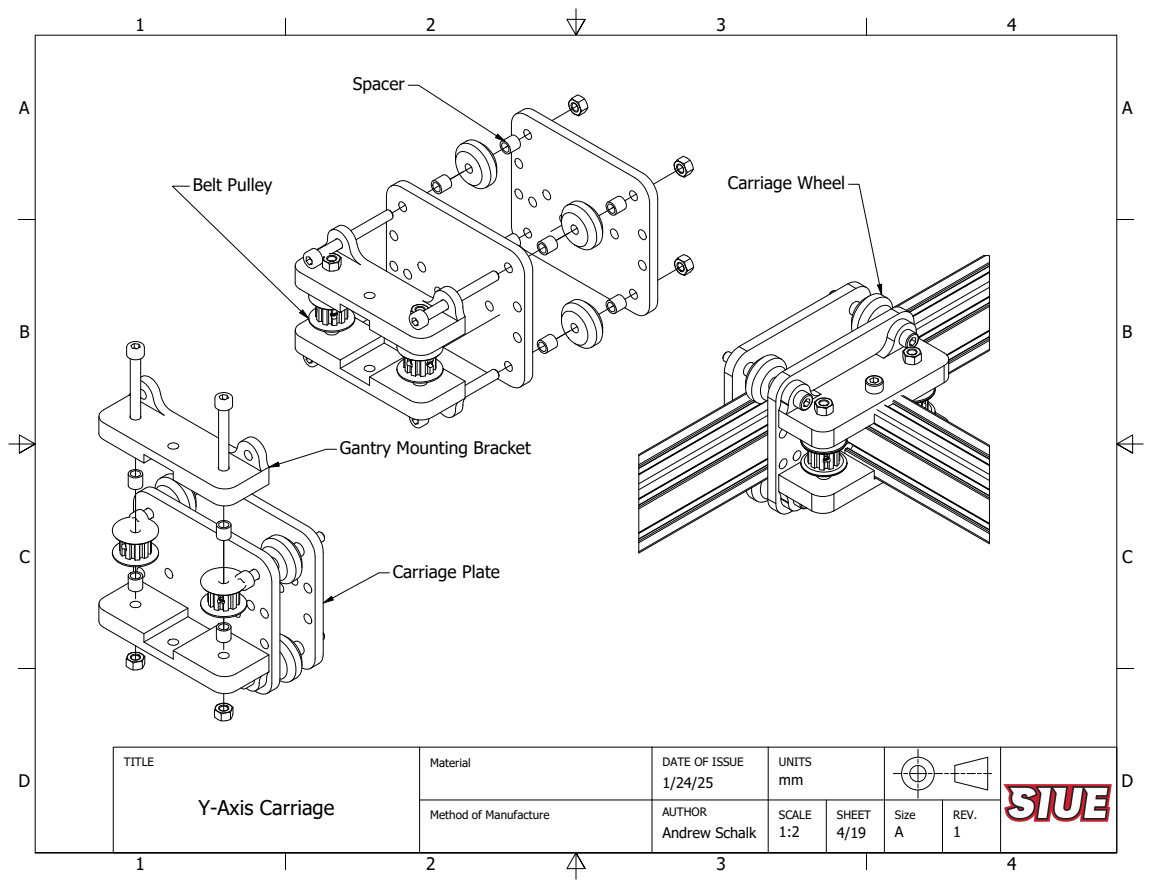
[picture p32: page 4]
Belt Pulley; Carriage Plate; Carriage Wheel

Gantry Mounting Bracket

TITLE Y-Axis Carriage | Material | DATE OF ISSUE 1/24/25 | UNITS mm

Method of Manufacture | AUTHOR | SCALE 1:2 | SHEET | Size | REV.

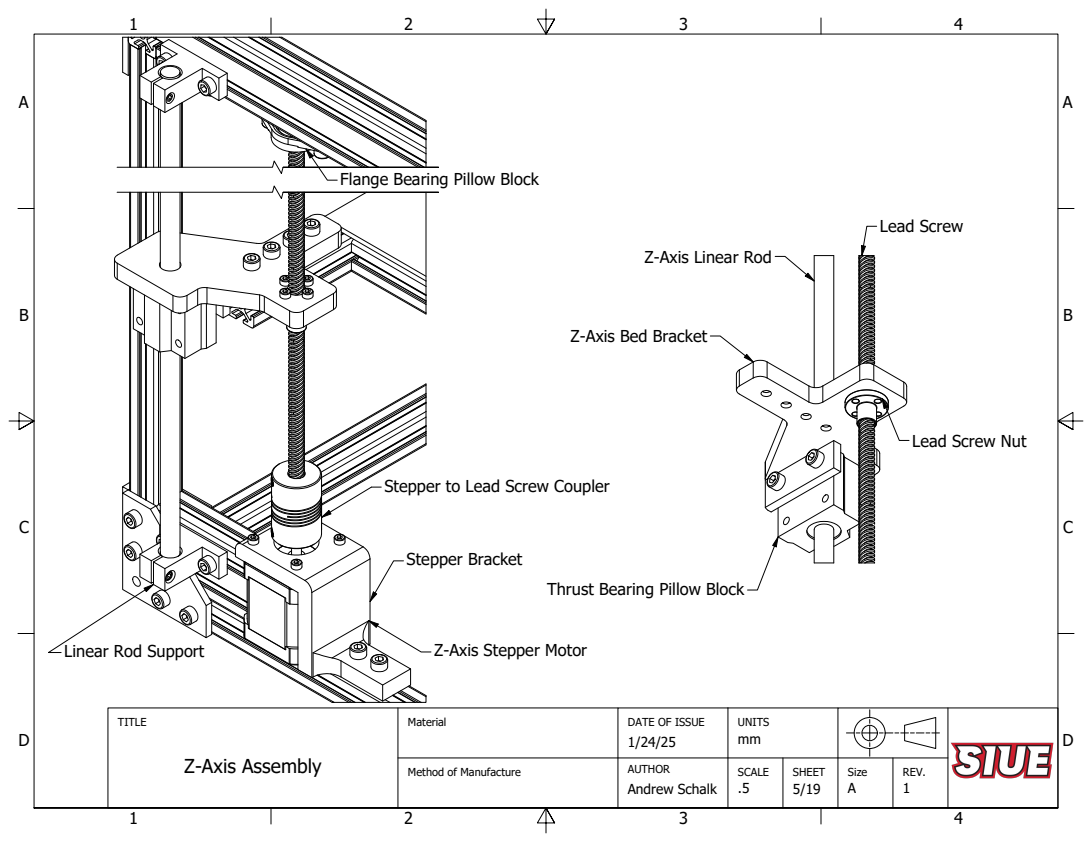
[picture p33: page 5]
Lead Screw; Stepper Bracket

Flange Bearing Pillow Block

Z-Axis Linear Rod

Z-Axis Bed Bracket

Lead Screw Nut

Stepper to Lead Screw Coupler

Thrust Bearing Pillow Block

Linear Rod Support

Z-Axis Stepper Motor

TITLE Z-Axis Assembly | Material | DATE OF ISSUE 1/24/25 | UNITS mm

Method of Manufacture | AUTHOR | SCALE | SHEET | Size | REV.

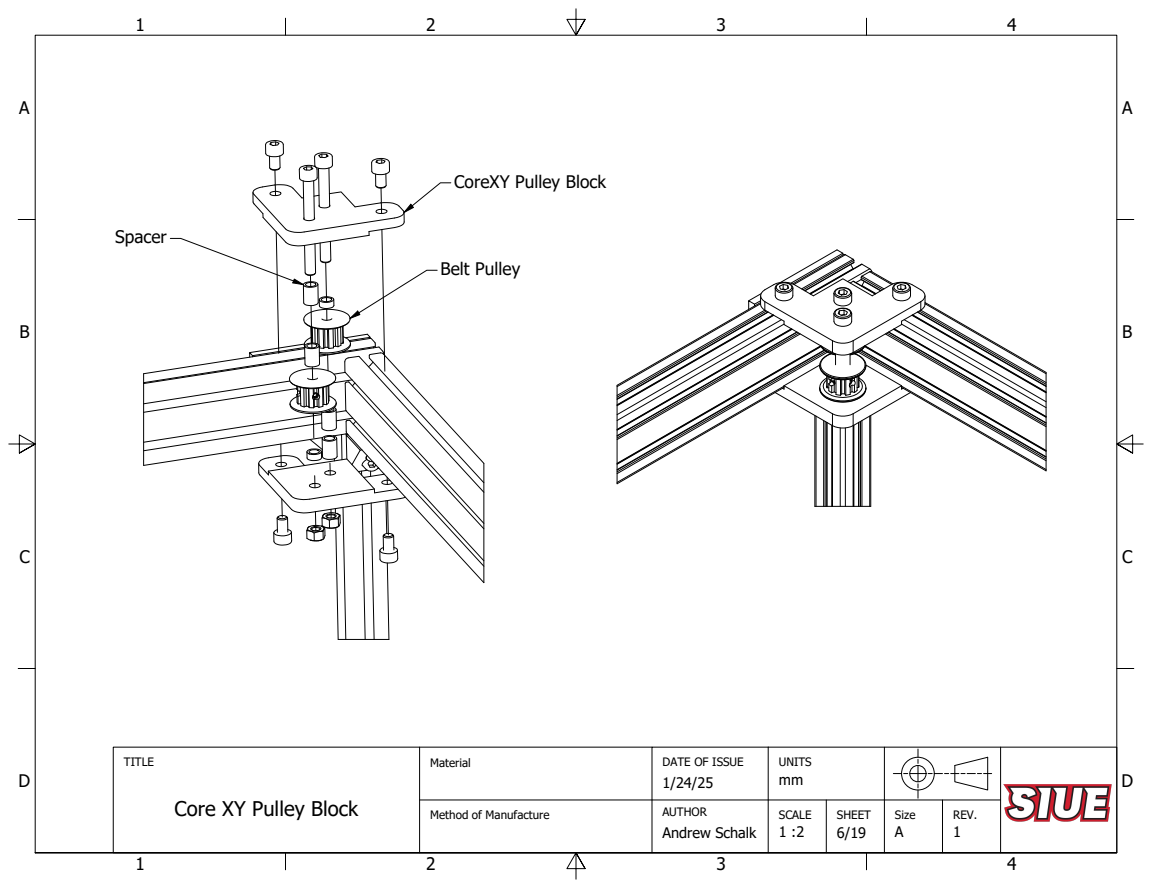
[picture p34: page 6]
Belt Pulley

CoreXY Pulley Block

TITLE Core XY Pulley Block | Material | DATE OF ISSUE 1/24/25 | UNITS mm

Method of Manufacture | AUTHOR | SCALE 1 :2 | SHEET | Size | REV.

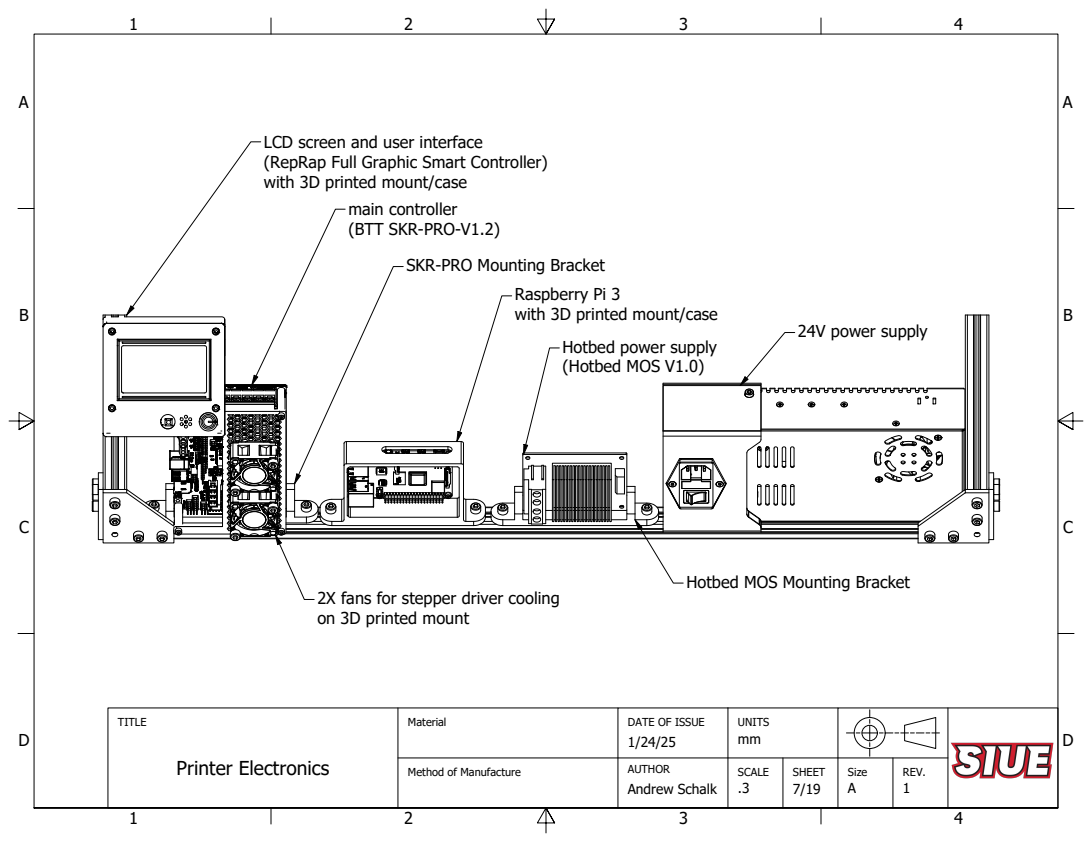
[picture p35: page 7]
Printer Electronics; SCALE; 24V power supply

LCD screen and user interface
(RepRap Full Graphic Smart Controller)
with 3D printed mount/case

main controller
(BTT SKR-PRO-V1.2)

SKR-PRO Mounting Bracket

Raspberry Pi 3

Hotbed power supply
(Hotbed MOS V1.0)

Hotbed MOS Mounting Bracket

2X fans for stepper driver cooling
on 3D printed mount

DATE OF ISSUE

Method of Manufacture

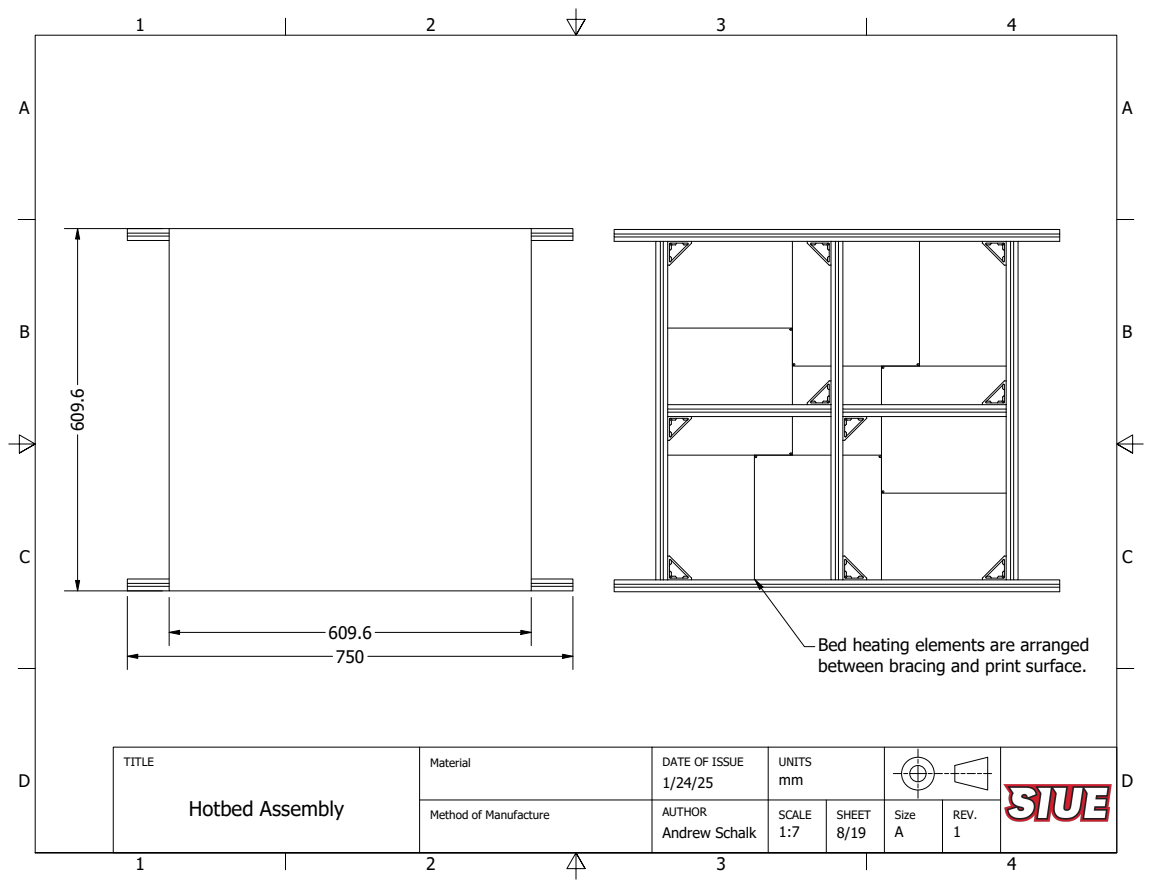
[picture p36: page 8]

Bed heating elements are arranged
between bracing and print surface.

TITLE Hotbed Assembly | Material | DATE OF ISSUE 1/24/25 | UNITS mm

Method of Manufacture | AUTHOR | SCALE 1:7 | SHEET | Size | REV.

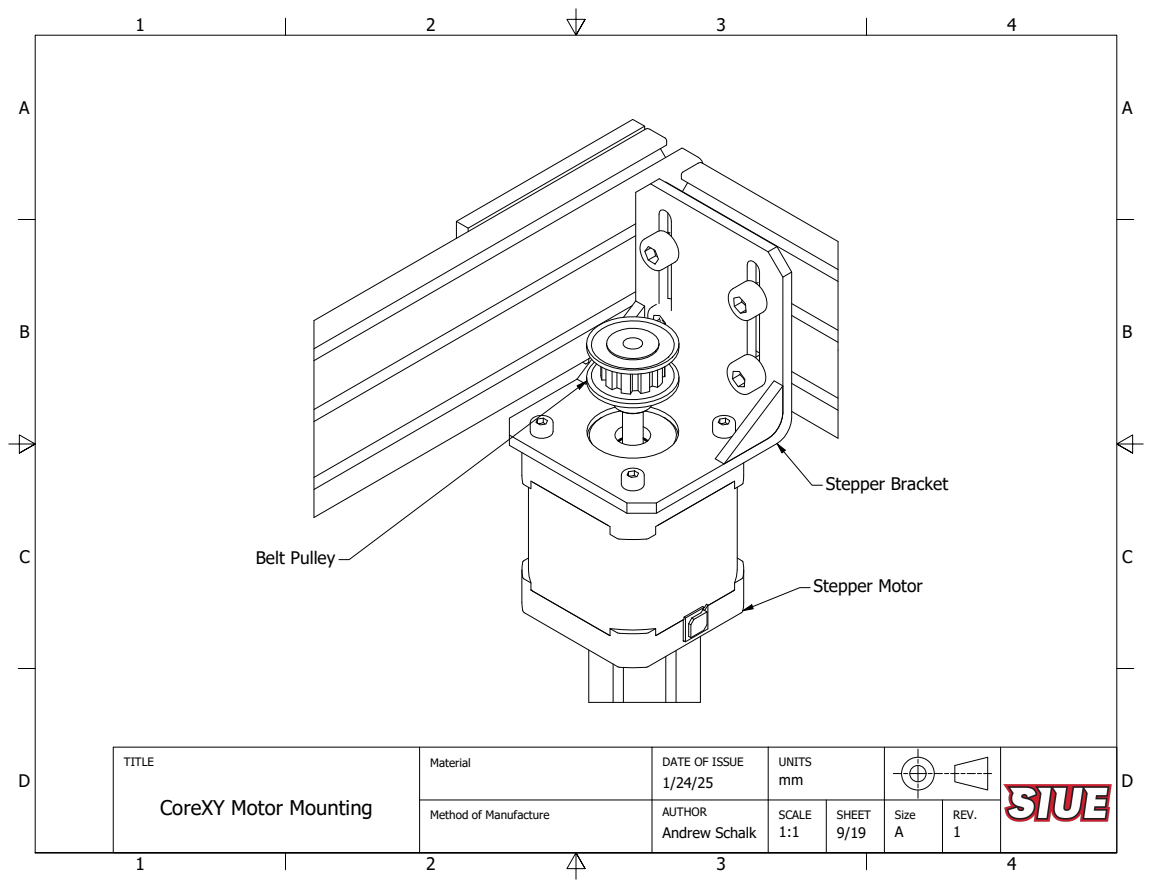
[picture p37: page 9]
Stepper Motor; Stepper Bracket; Belt Pulley

TITLE CoreXY Motor Mounting | Material | DATE OF ISSUE 1/24/25 | UNITS mm

Method of Manufacture | AUTHOR | SCALE 1:1 | SHEET | Size | REV.

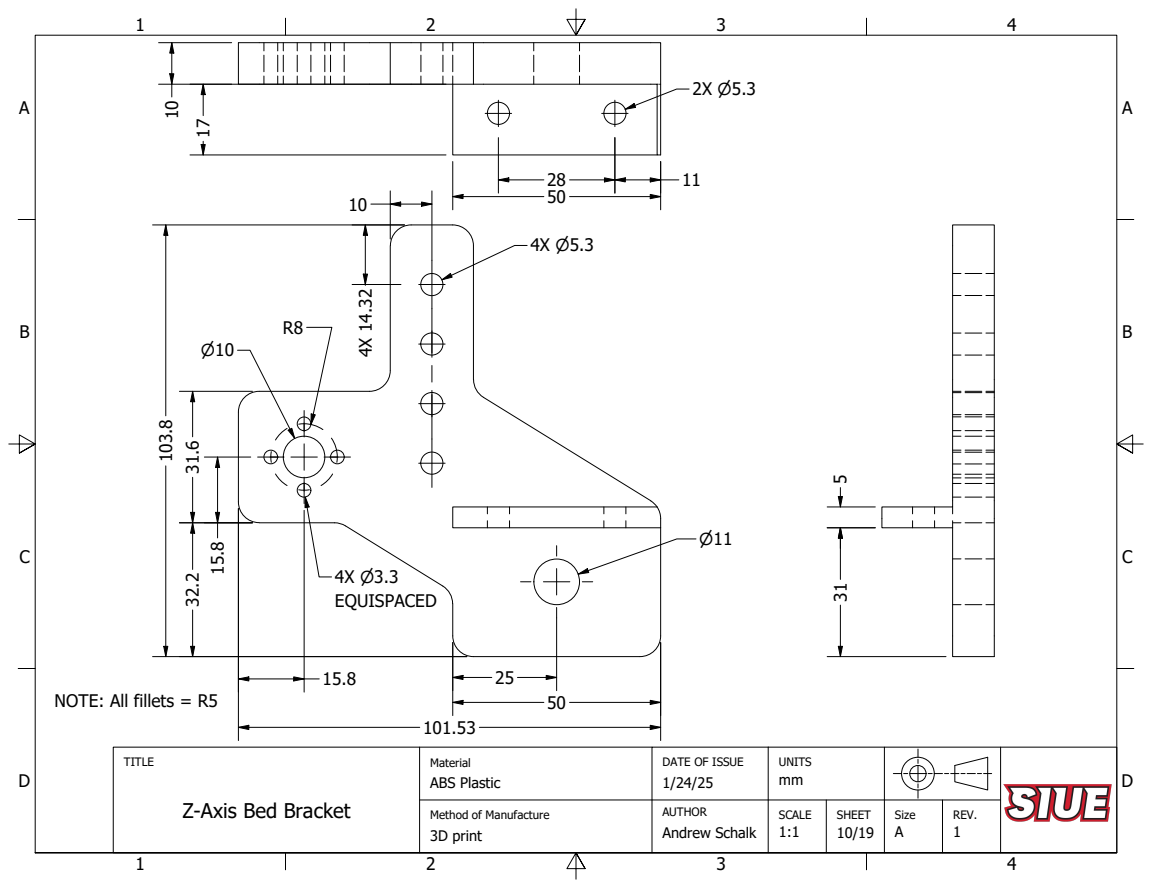
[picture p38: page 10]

NOTE: All fillets = R5

TITLE Z-Axis Bed Bracket | Material ABS Plastic | DATE OF ISSUE 1/24/25 | UNITS mm

Method of Manufacture 3D print | AUTHOR | SCALE 1:1 | SHEET | Size | REV.

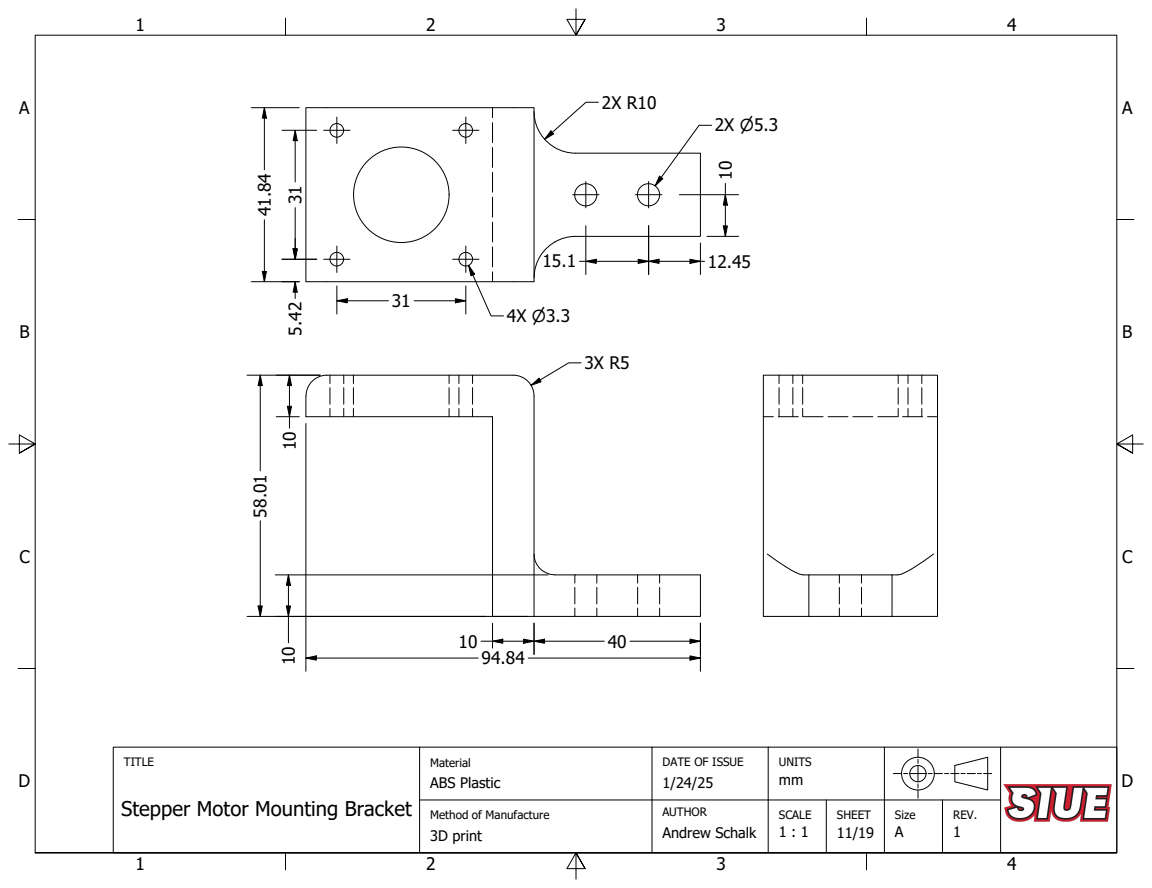
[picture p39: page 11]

TITLE Stepper Motor Mounting Bracket | Material ABS Plastic | DATE OF ISSUE 1/24/25 | UNITS mm

Method of Manufacture | AUTHOR | SCALE 1 : 1 | SHEET | Size | REV.

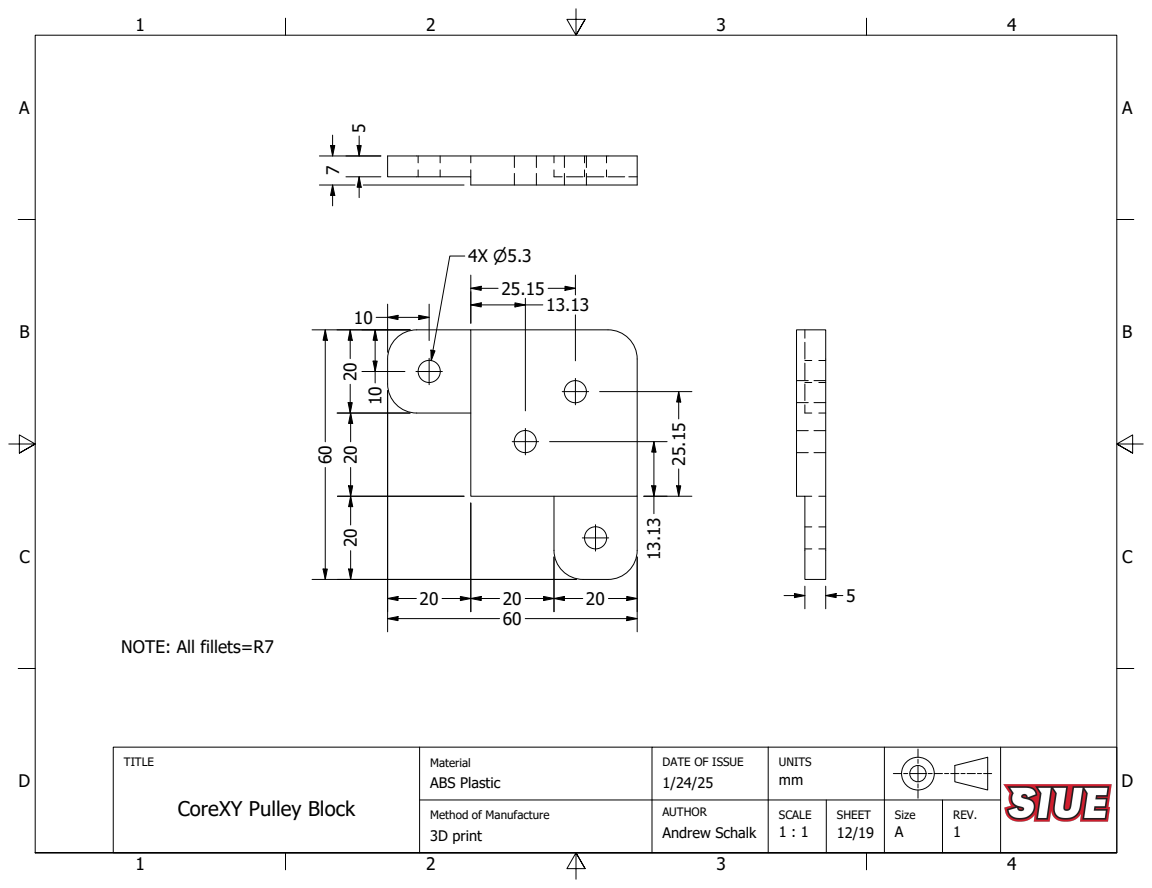
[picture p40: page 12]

NOTE: All fillets=R7

TITLE CoreXY Pulley Block | Material ABS Plastic | DATE OF ISSUE 1/24/25 | UNITS mm

Method of Manufacture | AUTHOR | SCALE 1 : 1 | SHEET | Size | REV.

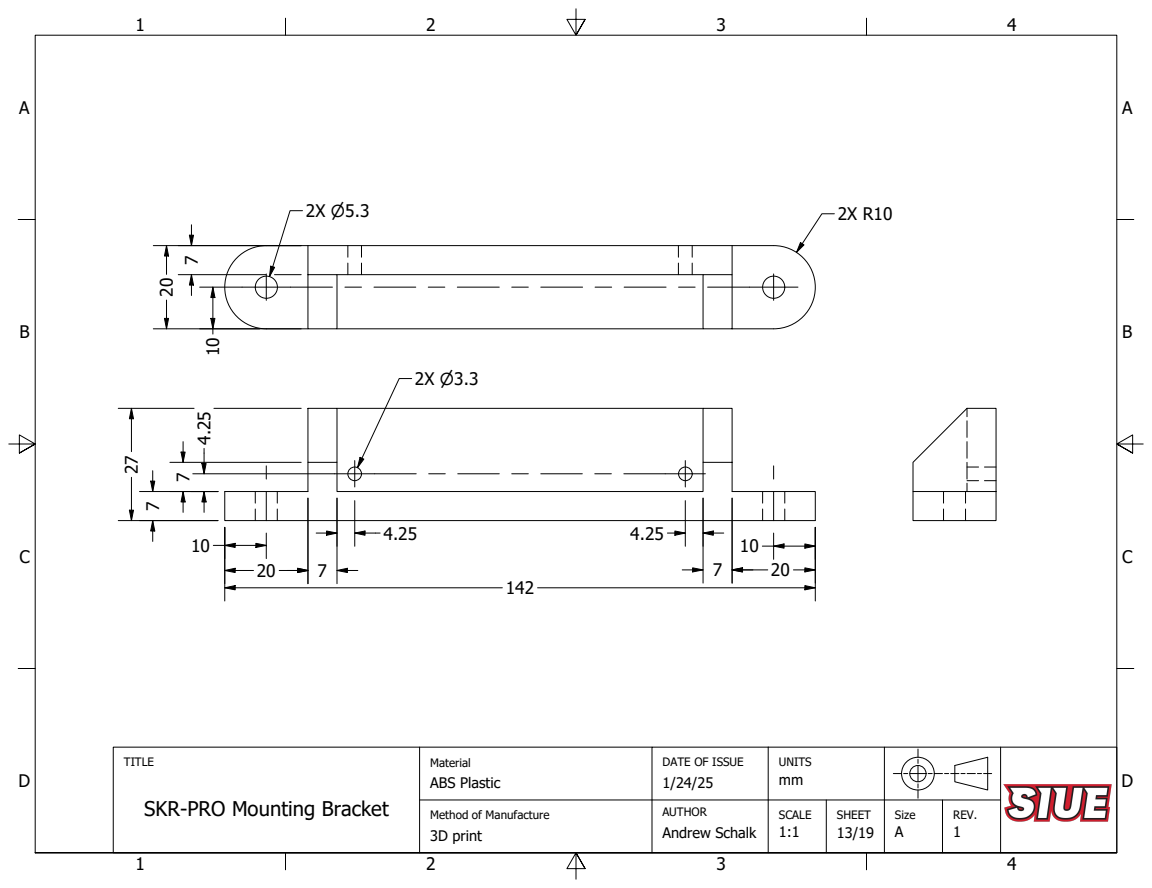
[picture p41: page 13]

TITLE SKR-PRO Mounting Bracket | Material ABS Plastic | DATE OF ISSUE 1/24/25 | UNITS mm

Method of Manufacture | AUTHOR | SCALE 1:1 | SHEET | Size | REV.

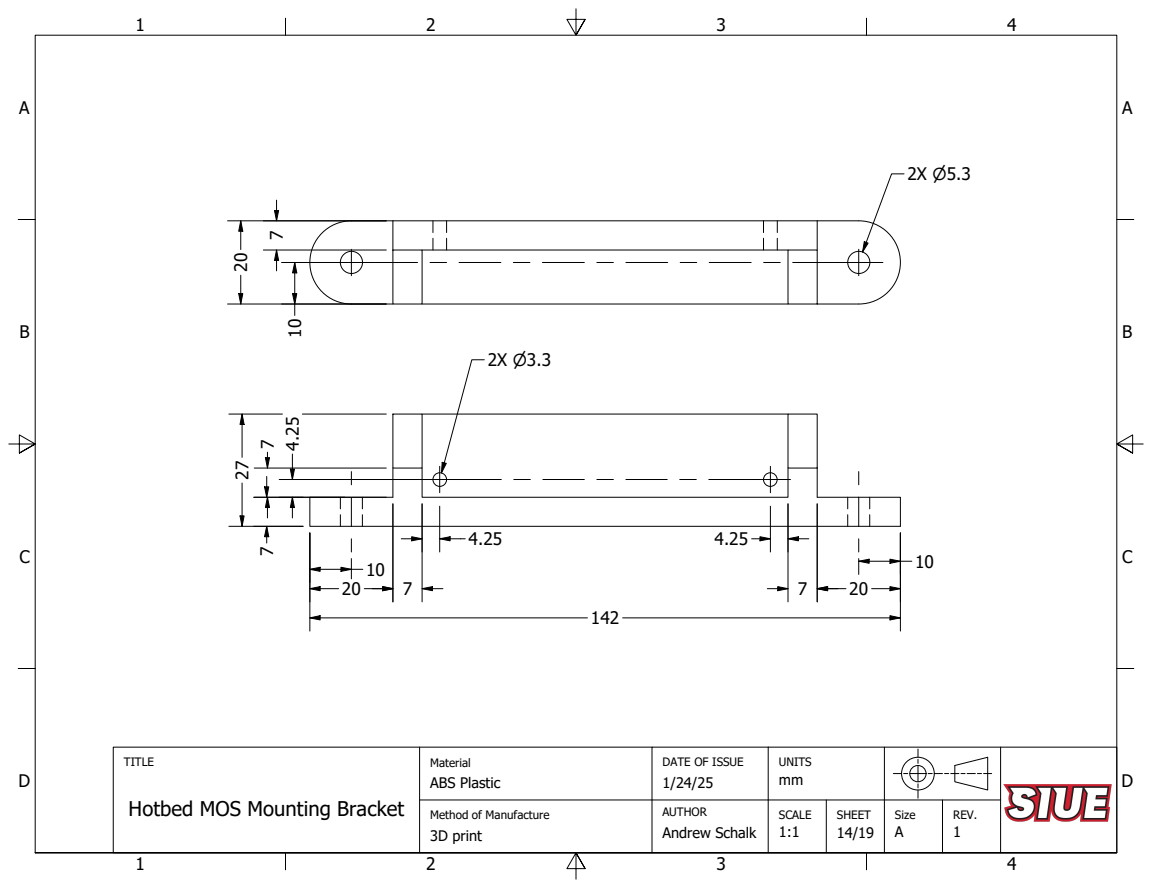
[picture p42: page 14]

TITLE Hotbed MOS Mounting Bracket | Material ABS Plastic | DATE OF ISSUE 1/24/25 | UNITS mm

Method of Manufacture | AUTHOR | SCALE 1:1 | SHEET | Size | REV.

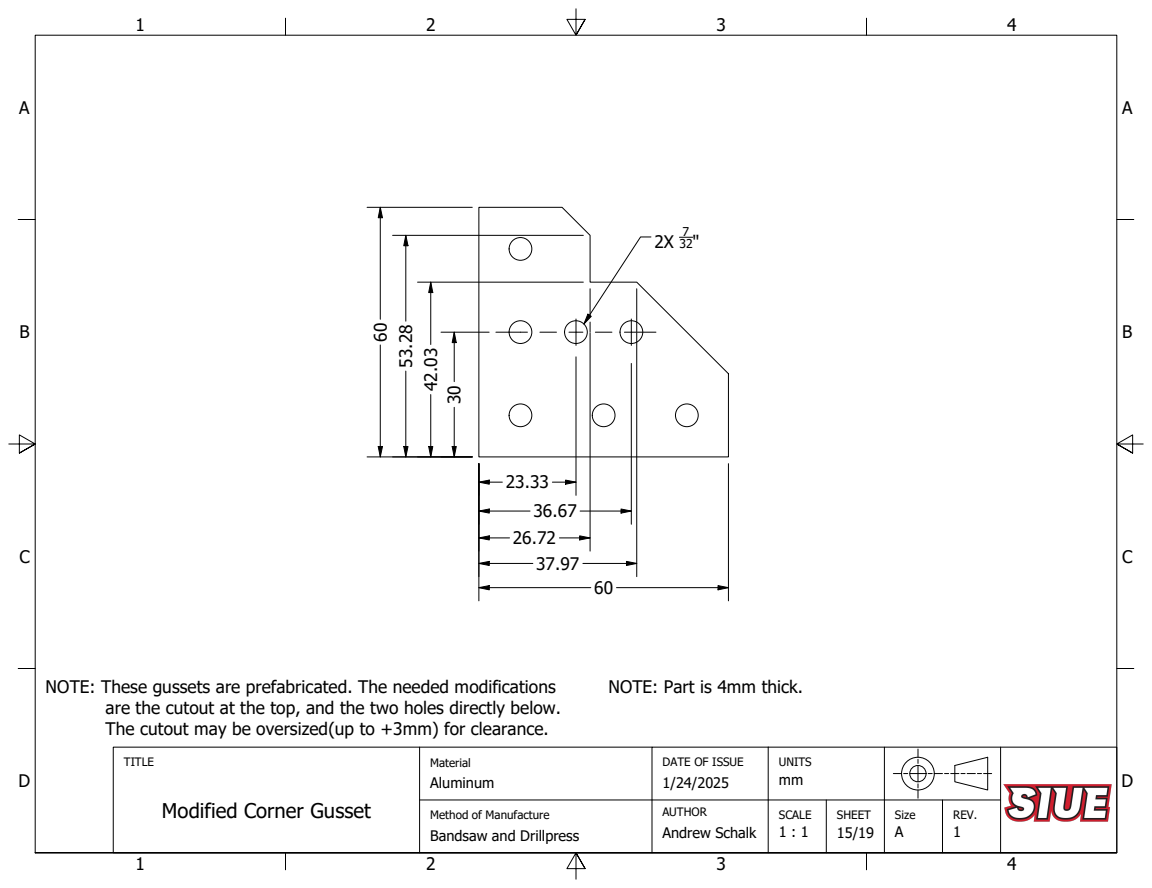
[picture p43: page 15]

NOTE: These gussets are prefabricated. The needed modifications

NOTE: Part is 4mm thick.

are the cutout at the top, and the two holes directly below.
The cutout may be oversized(up to +3mm) for clearance.

TITLE Modified Corner Gusset | Material Aluminum | DATE OF ISSUE 1/24/2025 | UNITS mm

Method of Manufacture Bandsaw and Drillpress | AUTHOR | SCALE 1 : 1 | SHEET | Size | REV.

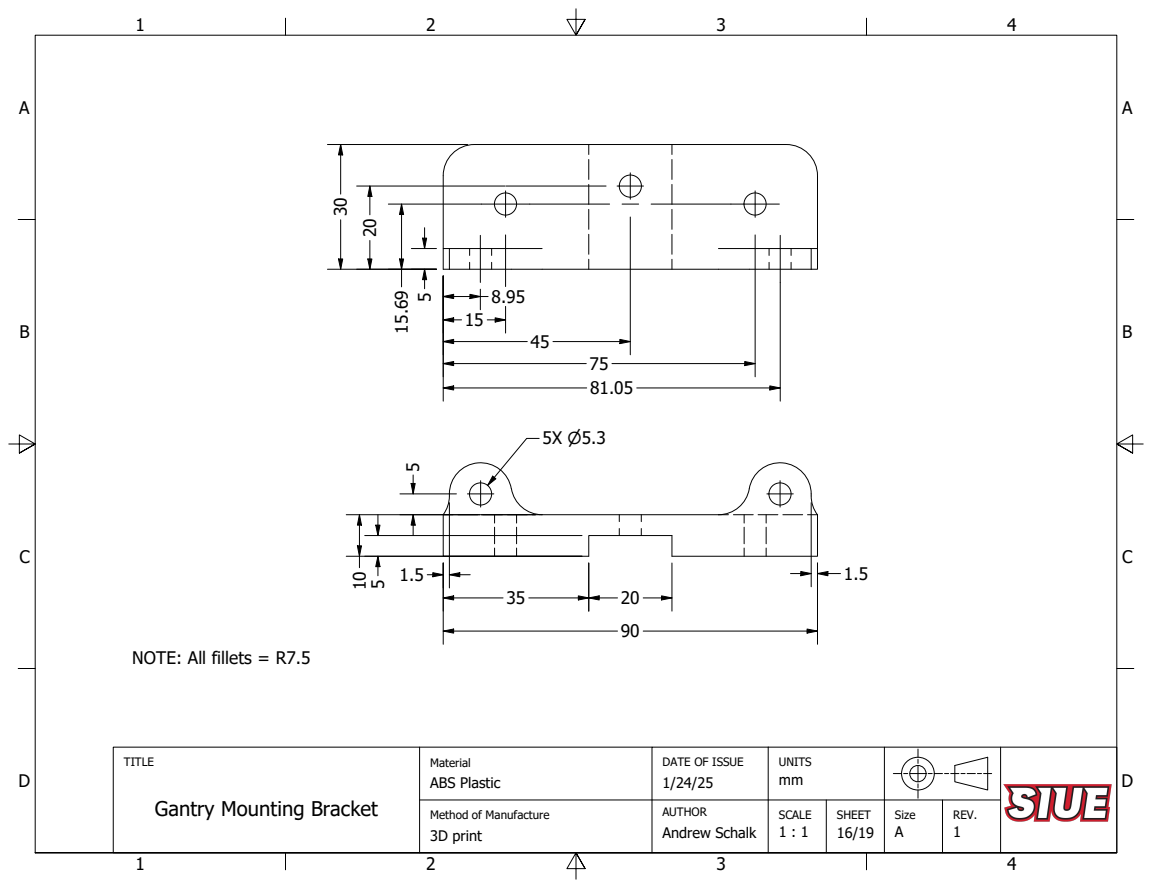
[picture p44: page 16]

NOTE: All fillets = R7.5

TITLE Gantry Mounting Bracket | Material ABS Plastic | DATE OF ISSUE 1/24/25 | UNITS mm

Method of Manufacture | AUTHOR | SCALE 1 : 1 | SHEET | Size | REV.

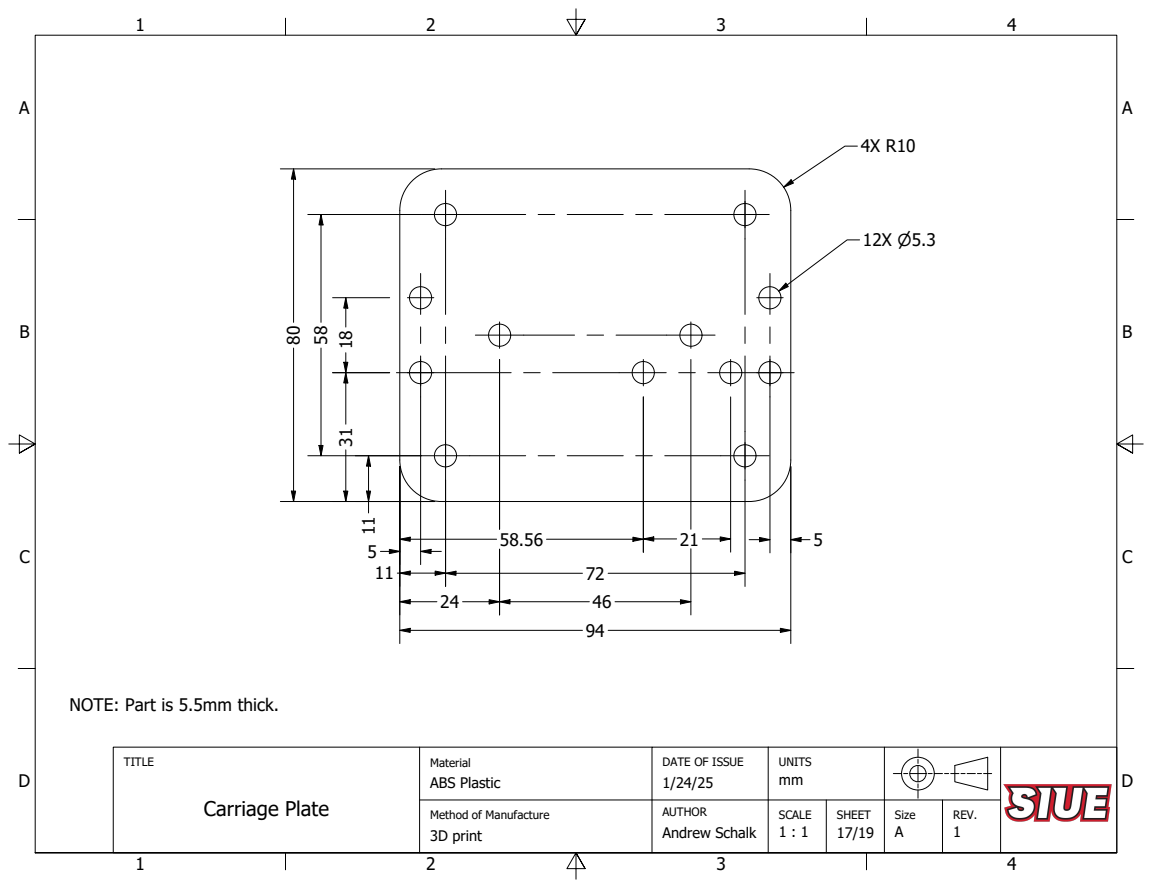
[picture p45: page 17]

NOTE: Part is 5.5mm thick.

TITLE Carriage Plate | Material ABS Plastic | DATE OF ISSUE 1/24/25 | UNITS mm

Method of Manufacture | AUTHOR | SCALE 1 : 1 | SHEET | Size | REV.

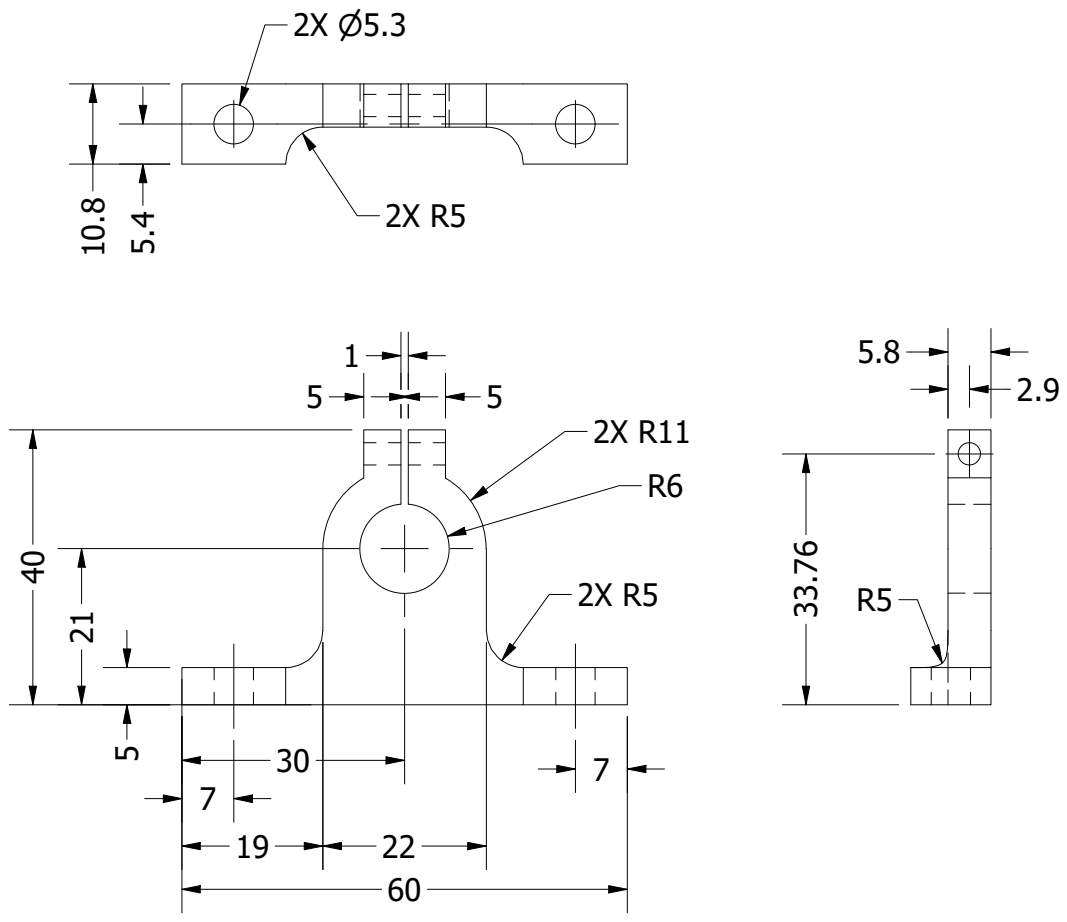
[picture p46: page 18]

TITLE Hot End Mount | Material ABS Plastic | DATE OF ISSUE 1/24/25 | UNITS mm

Method of Manufacture | AUTHOR | SCALE 1 : 1 | SHEET | Size | REV.

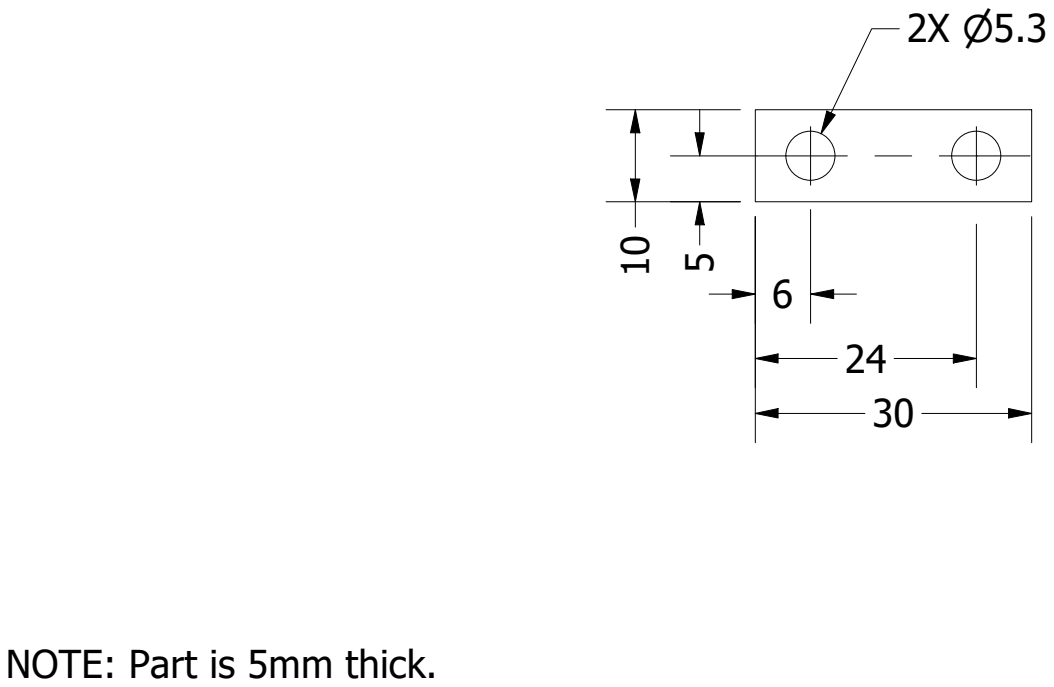
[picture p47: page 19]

NOTE: Part is 5mm thick.

TITLE Belt Fastener | Material ABS Plastic | DATE OF ISSUE 1/24/25 | UNITS mm

Method of Manufacture | AUTHOR | SCALE 1 : 1 | SHEET | Size | REV.

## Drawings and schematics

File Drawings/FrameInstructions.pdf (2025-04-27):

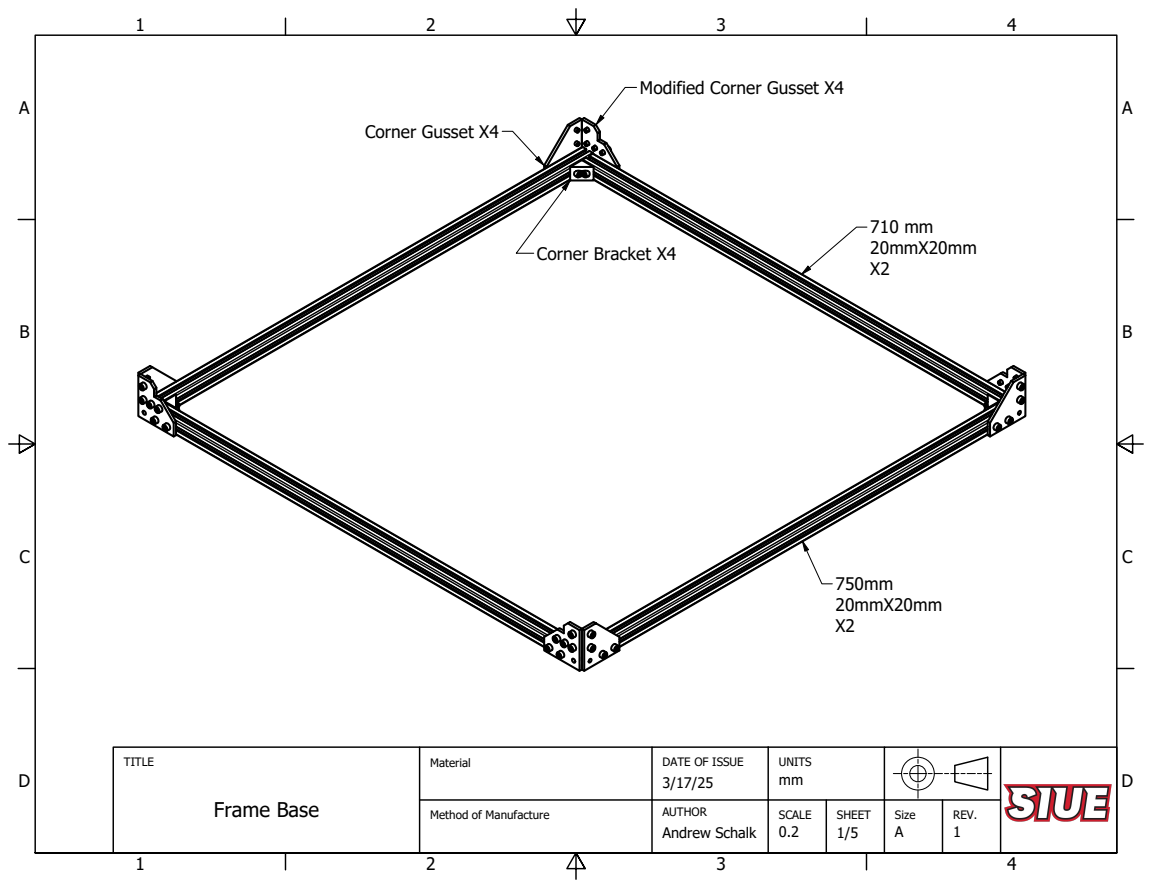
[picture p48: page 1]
Corner Gusset X4; Corner Bracket X4

Modified Corner Gusset X4

TITLE Frame Base | Material | DATE OF ISSUE 3/17/25 | UNITS mm

Method of Manufacture | AUTHOR Andrew Schalk | SCALE 0.2 | SHEET | Size A | REV.

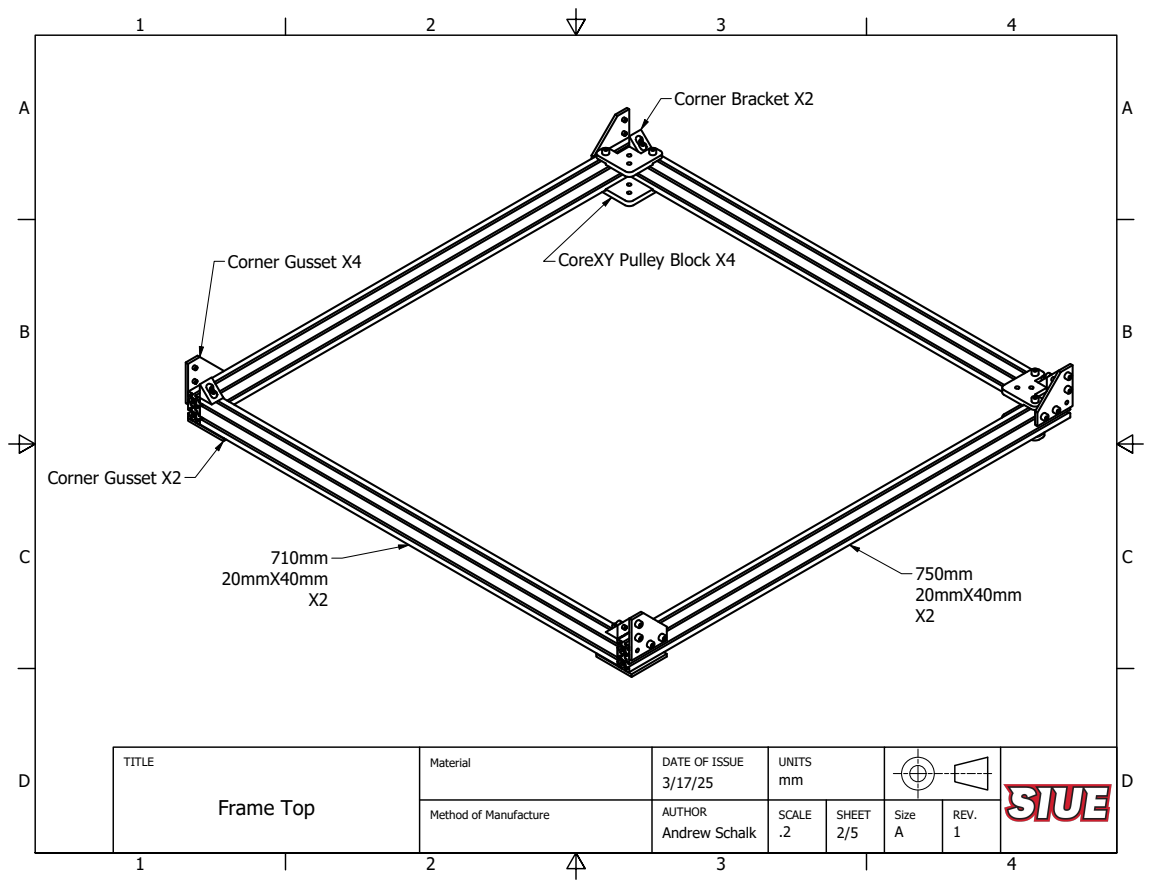
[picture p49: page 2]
Corner Gusset X4; Corner Gusset X2; Corner Bracket X2

CoreXY Pulley Block X4

TITLE Frame Top | Material | DATE OF ISSUE 3/17/25 | UNITS mm

Method of Manufacture | AUTHOR | SCALE | SHEET | Size | REV.

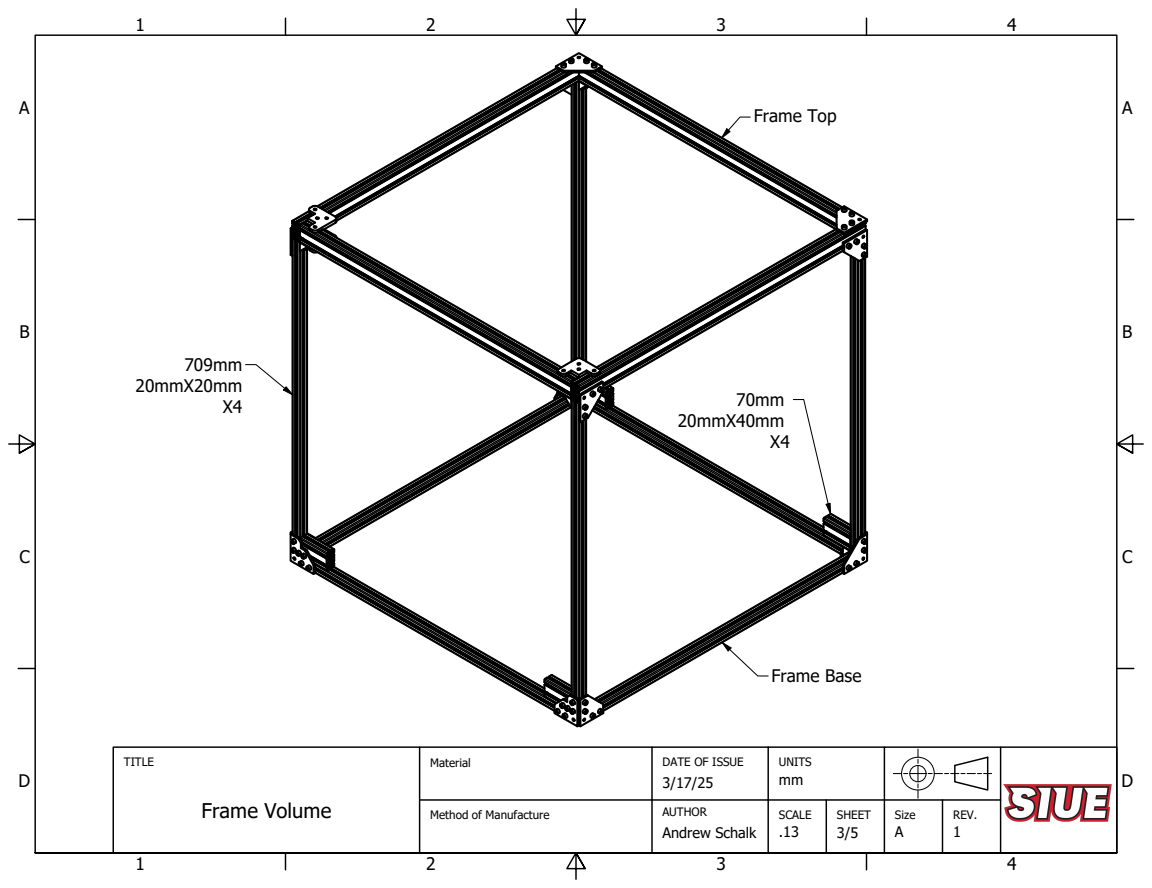
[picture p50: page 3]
Frame Base; Frame Top

TITLE Frame Volume | Material | DATE OF ISSUE 3/17/25 | UNITS mm

Method of Manufacture | AUTHOR | SCALE | SHEET | Size | REV.

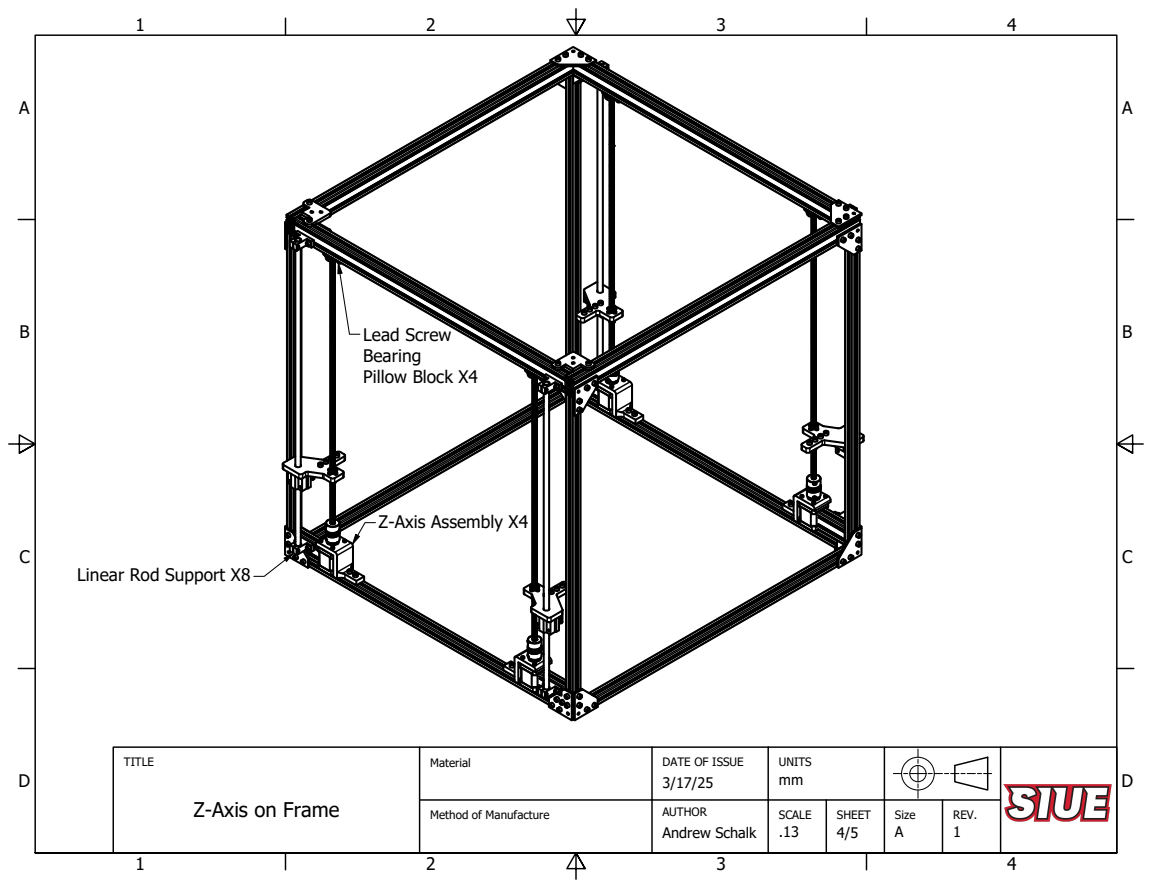
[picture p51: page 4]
Z-Axis on Frame; SCALE; Z-Axis Assembly X4; Lead Screw; Pillow Block X4

Linear Rod Support X8

DATE OF ISSUE

Method of Manufacture

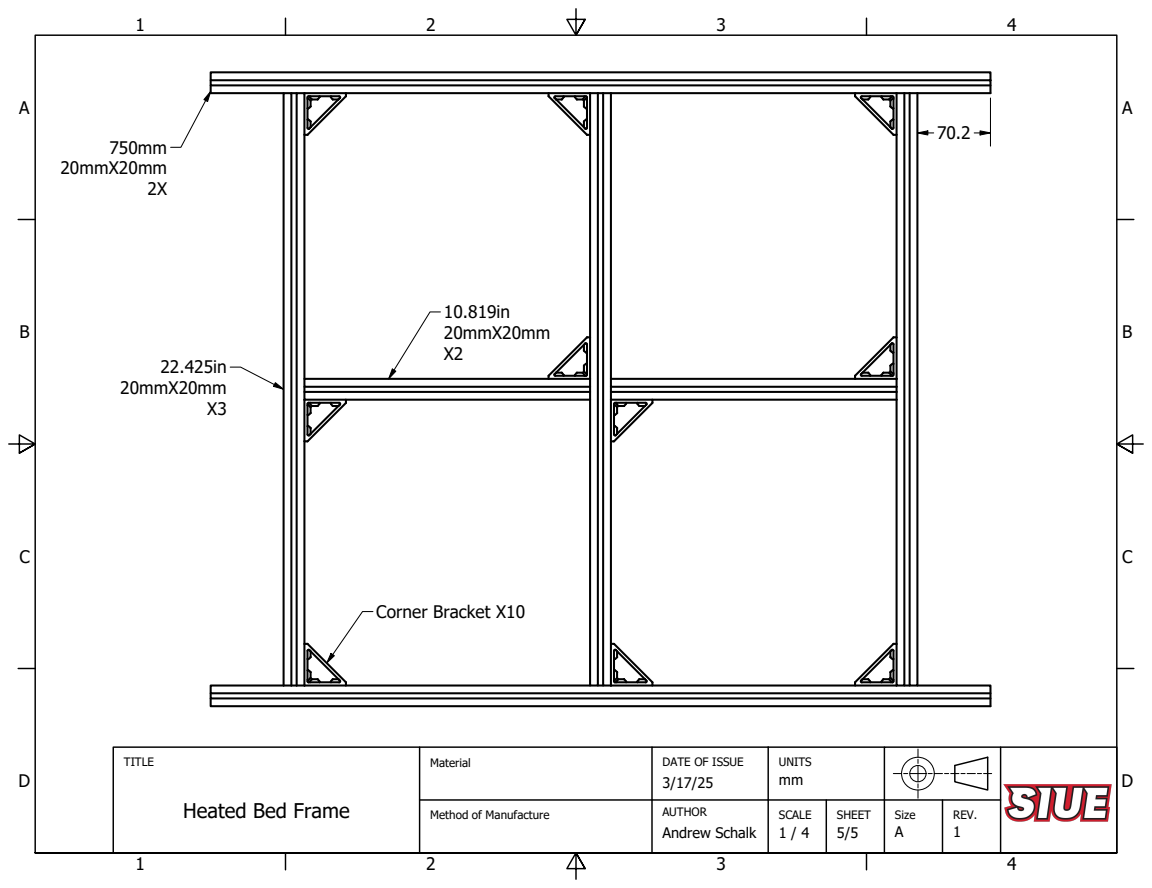
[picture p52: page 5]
Corner Bracket X10

TITLE Heated Bed Frame | Material | DATE OF ISSUE 3/17/25 | UNITS mm

Method of Manufacture | AUTHOR | SCALE 1 / 4 | SHEET | Size | REV.

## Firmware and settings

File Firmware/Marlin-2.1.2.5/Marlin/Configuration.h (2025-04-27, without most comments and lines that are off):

#pragma once
#define CONFIGURATION_H_VERSION 02010205
#define STRING_CONFIG_H_AUTHOR "Andrew Schalk" // Who made the changes.
#define SHOW_BOOTSCREEN
#define SHOW_CUSTOM_BOOTSCREEN
  #define MOTHERBOARD BOARD_BTT_SKR_PRO_V1_2
#define SERIAL_PORT 1
#define BAUDRATE 115200
#define SERIAL_PORT_2 -1
#define CUSTOM_MACHINE_NAME "LibrePrint XL"
#define X_DRIVER_TYPE  TMC2209
#define Y_DRIVER_TYPE  TMC2209
#define Z_DRIVER_TYPE  TMC2209
#define Z2_DRIVER_TYPE TMC2209
#define E0_DRIVER_TYPE TMC2209
#define EXTRUDERS 1
#define DEFAULT_NOMINAL_FILAMENT_DIA 1.75
#define TEMP_SENSOR_0 1
#define TEMP_SENSOR_1 0
#define TEMP_SENSOR_2 0
#define TEMP_SENSOR_3 0
#define TEMP_SENSOR_4 0
#define TEMP_SENSOR_5 0
#define TEMP_SENSOR_6 0
#define TEMP_SENSOR_7 0
#define TEMP_SENSOR_BED 1
#define TEMP_SENSOR_PROBE 0
#define TEMP_SENSOR_CHAMBER 0
#define TEMP_SENSOR_COOLER 0
#define TEMP_SENSOR_BOARD 0
#define TEMP_SENSOR_REDUNDANT 0
#define DUMMY_THERMISTOR_998_VALUE  25
#define DUMMY_THERMISTOR_999_VALUE 100
#if TEMP_SENSOR_IS_MAX_TC(0)
  #define MAX31865_SENSOR_OHMS_0      100 // (Ω) Typically 100 or 1000 (PT100 or PT1000)
  #define MAX31865_CALIBRATION_OHMS_0 430 // (Ω) Typically 430 for Adafruit PT100; 4300 for Adafruit PT1000
#endif
#if TEMP_SENSOR_IS_MAX_TC(1)
  #define MAX31865_SENSOR_OHMS_1      100
  #define MAX31865_CALIBRATION_OHMS_1 430
#endif
#if TEMP_SENSOR_IS_MAX_TC(2)
  #define MAX31865_SENSOR_OHMS_2      100
  #define MAX31865_CALIBRATION_OHMS_2 430
#endif
#if HAS_E_TEMP_SENSOR
  #define TEMP_RESIDENCY_TIME          9  // (seconds) Time to wait for hotend to "settle" in M109
  #define TEMP_WINDOW                  1  // (°C) Temperature proximity for the "temperature reached" timer
  #define TEMP_HYSTERESIS              4  // (°C) Temperature proximity considered "close enough" to the target
#endif
#if TEMP_SENSOR_BED
  #define TEMP_BED_RESIDENCY_TIME     10  // (seconds) Time to wait for bed to "settle" in M190
  #define TEMP_BED_WINDOW              1  // (°C) Temperature proximity for the "temperature reached" timer
  #define TEMP_BED_HYSTERESIS          3  // (°C) Temperature proximity considered "close enough" to the target
#endif
#if TEMP_SENSOR_CHAMBER
  #define TEMP_CHAMBER_RESIDENCY_TIME 10  // (seconds) Time to wait for chamber to "settle" in M191
  #define TEMP_CHAMBER_WINDOW          1  // (°C) Temperature proximity for the "temperature reached" timer
  #define TEMP_CHAMBER_HYSTERESIS      3  // (°C) Temperature proximity considered "close enough" to the target
#endif
#if TEMP_SENSOR_REDUNDANT
  #define TEMP_SENSOR_REDUNDANT_SOURCE    E1  // The sensor that will provide the redundant reading.
  #define TEMP_SENSOR_REDUNDANT_TARGET    E0  // The sensor that we are providing a redundant reading for.
  #define TEMP_SENSOR_REDUNDANT_MAX_DIFF  10  // (°C) Temperature difference that will trigger a print abort.
#endif
#define HEATER_0_MINTEMP   5
#define HEATER_1_MINTEMP   5
#define HEATER_2_MINTEMP   5
#define HEATER_3_MINTEMP   5
#define HEATER_4_MINTEMP   5
#define HEATER_5_MINTEMP   5
#define HEATER_6_MINTEMP   5
#define HEATER_7_MINTEMP   5
#define BED_MINTEMP        5
#define CHAMBER_MINTEMP    5
#define HEATER_0_MAXTEMP 300
#define HEATER_1_MAXTEMP 275
#define HEATER_2_MAXTEMP 275
#define HEATER_3_MAXTEMP 275
#define HEATER_4_MAXTEMP 275
#define HEATER_5_MAXTEMP 275
#define HEATER_6_MAXTEMP 275
#define HEATER_7_MAXTEMP 275
#define BED_MAXTEMP      150
#define CHAMBER_MAXTEMP  60
#define HOTEND_OVERSHOOT 15   // (°C) Forbid temperatures over MAXTEMP - OVERSHOOT
#define BED_OVERSHOOT    10   // (°C) Forbid temperatures over MAXTEMP - OVERSHOOT
#define COOLER_OVERSHOOT  2   // (°C) Forbid temperatures closer than OVERSHOOT
#define PIDTEMP           // See the PID Tuning Guide at https://reprap.org/wiki/PID_Tuning
#define PID_MAX  255      // Limit hotend current while PID is active (see PID_FUNCTIONAL_RANGE below); 255=full current
#define PID_K1     0.95   // Smoothing factor within any PID loop
    #define DEFAULT_Kp  21.19
    #define DEFAULT_Ki   1.63
    #define DEFAULT_Kd 68.64
#define MAX_BED_POWER 255 // limits duty cycle to bed; 255=full current
#define MAX_CHAMBER_POWER 255 // limits duty cycle to chamber heater; 255=full current
  #define PID_FUNCTIONAL_RANGE 10 // If the temperature difference between the target temperature and the actual temperature
#define PREVENT_COLD_EXTRUSION
#define EXTRUDE_MINTEMP 170
#define PREVENT_LENGTHY_EXTRUDE
#define EXTRUDE_MAXLENGTH 200
#define THERMAL_PROTECTION_HOTENDS // Enable thermal protection for all extruders
#define THERMAL_PROTECTION_BED     // Enable thermal protection for the heated bed
#define THERMAL_PROTECTION_CHAMBER // Enable thermal protection for the heated chamber
#define THERMAL_PROTECTION_COOLER  // Enable thermal protection for the laser cooling
#define COREXY
#define USE_XMIN_PLUG
#define USE_YMIN_PLUG
#define USE_ZMIN_PLUG
#define ENDSTOPPULLUPS
#define X_MIN_ENDSTOP_INVERTING false // Set to true to invert the logic of the endstop.
#define Y_MIN_ENDSTOP_INVERTING false // Set to true to invert the logic of the endstop.
#define Z_MIN_ENDSTOP_INVERTING false // Set to true to invert the logic of the endstop.
#define I_MIN_ENDSTOP_INVERTING false // Set to true to invert the logic of the endstop.
#define J_MIN_ENDSTOP_INVERTING false // Set to true to invert the logic of the endstop.
#define K_MIN_ENDSTOP_INVERTING false // Set to true to invert the logic of the endstop.
#define U_MIN_ENDSTOP_INVERTING false // Set to true to invert the logic of the endstop.
#define V_MIN_ENDSTOP_INVERTING false // Set to true to invert the logic of the endstop.
#define W_MIN_ENDSTOP_INVERTING false // Set to true to invert the logic of the endstop.
#define X_MAX_ENDSTOP_INVERTING false // Set to true to invert the logic of the endstop.
#define Y_MAX_ENDSTOP_INVERTING false // Set to true to invert the logic of the endstop.
#define Z_MAX_ENDSTOP_INVERTING false // Set to true to invert the logic of the endstop.
#define I_MAX_ENDSTOP_INVERTING false // Set to true to invert the logic of the endstop.
#define J_MAX_ENDSTOP_INVERTING false // Set to true to invert the logic of the endstop.
#define K_MAX_ENDSTOP_INVERTING false // Set to true to invert the logic of the endstop.
#define U_MAX_ENDSTOP_INVERTING false // Set to true to invert the logic of the endstop.
#define V_MAX_ENDSTOP_INVERTING false // Set to true to invert the logic of the endstop.
#define W_MAX_ENDSTOP_INVERTING false // Set to true to invert the logic of the endstop.
#define Z_MIN_PROBE_ENDSTOP_INVERTING false // Set to true to invert the logic of the probe.
#define DEFAULT_AXIS_STEPS_PER_UNIT   { 80, 80, 800, 97 }
#define DEFAULT_MAX_FEEDRATE          { 300, 300, 5, 25 }
#define DEFAULT_MAX_ACCELERATION      { 3000, 3000, 100, 10000 }
#define DEFAULT_ACCELERATION          3000    // X, Y, Z and E acceleration for printing moves
#define DEFAULT_RETRACT_ACCELERATION  3000    // E acceleration for retracts
#define DEFAULT_TRAVEL_ACCELERATION   3000    // X, Y, Z acceleration for travel (non printing) moves
#define DEFAULT_EJERK    5.0  // May be used by Linear Advance
  #define JUNCTION_DEVIATION_MM 0.013 // (mm) Distance from real junction edge
  #define JD_HANDLE_SMALL_SEGMENTS    // Use curvature estimation instead of just the junction angle
#define S_CURVE_ACCELERATION
#define USE_PROBE_FOR_Z_HOMING
#define BLTOUCH
#define NOZZLE_TO_PROBE_OFFSET { 45, 22, -.4 }
#define PROBING_MARGIN 100
#define XY_PROBE_FEEDRATE (133*60)
#define Z_PROBE_FEEDRATE_FAST (4*60)
#define Z_PROBE_FEEDRATE_SLOW (Z_PROBE_FEEDRATE_FAST / 2)
#define Z_CLEARANCE_DEPLOY_PROBE   10 // (mm) Z Clearance for Deploy/Stow
#define Z_CLEARANCE_BETWEEN_PROBES  5 // (mm) Z Clearance between probe points
#define Z_CLEARANCE_MULTI_PROBE     5 // (mm) Z Clearance between multiple probes
#define Z_AFTER_PROBING           10 // (mm) Z position after probing is done
#define Z_PROBE_LOW_POINT          -2 // (mm) Farthest distance below the trigger-point to go before stopping
#define Z_PROBE_OFFSET_RANGE_MIN -20
#define Z_PROBE_OFFSET_RANGE_MAX 20
#define X_ENABLE_ON 0
#define Y_ENABLE_ON 0
#define Z_ENABLE_ON 0
#define E_ENABLE_ON 0 // For all extruders
#define DISABLE_OTHER_EXTRUDERS   // Keep only the active extruder enabled
#define INVERT_X_DIR true
#define INVERT_Y_DIR true
#define INVERT_Z_DIR false
#define INVERT_E0_DIR false
#define INVERT_E1_DIR false
#define INVERT_E2_DIR false
#define INVERT_E3_DIR false
#define INVERT_E4_DIR false
#define INVERT_E5_DIR false
#define INVERT_E6_DIR false
#define INVERT_E7_DIR false
#define Z_AFTER_HOMING  10      // (mm) Height to move to after homing Z
#define X_HOME_DIR -1
#define Y_HOME_DIR -1
#define Z_HOME_DIR -1
#define X_BED_SIZE 540
#define Y_BED_SIZE 510
#define X_MIN_POS 0
#define Y_MIN_POS 0
#define Z_MIN_POS 0
#define X_MAX_POS X_BED_SIZE
#define Y_MAX_POS Y_BED_SIZE
#define Z_MAX_POS 545
#define MIN_SOFTWARE_ENDSTOPS
  #define MIN_SOFTWARE_ENDSTOP_X
  #define MIN_SOFTWARE_ENDSTOP_Y
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

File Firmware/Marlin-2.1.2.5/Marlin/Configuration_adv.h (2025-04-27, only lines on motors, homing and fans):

  #define CONTROLLER_FAN_PIN PE6           // Set a custom pin for the controller fan
#define E0_AUTO_FAN_PIN PE5
#define E1_AUTO_FAN_PIN -1
#define E2_AUTO_FAN_PIN -1
#define E3_AUTO_FAN_PIN -1
#define E4_AUTO_FAN_PIN -1
#define E5_AUTO_FAN_PIN -1
#define E6_AUTO_FAN_PIN -1
#define E7_AUTO_FAN_PIN -1
#define CHAMBER_AUTO_FAN_PIN -1
#define COOLER_AUTO_FAN_PIN PC8
#define HOMING_BUMP_MM      { 5, 5, 2 }       // (linear=mm, rotational=°) Backoff from endstops after first bump
#define HOMING_BUMP_DIVISOR { 2, 2, 4 }       // Re-Bump Speed Divisor (Divides the Homing Feedrate)
#define HOMING_BACKOFF_POST_MM { 0, 0, 10 }  // (linear=mm, rotational=°) Backoff from endstops after homing
#define MICROSTEP_MODES { 16, 16, 16, 16, 16, 16 } // [1,2,4,8,16]
  #define BABYSTEP_WITHOUT_HOMING
#define LIN_ADVANCE
    #define ADVANCE_K 1.1        // (mm) Compression length applying to all extruders
#define ADVANCED_PAUSE_FEATURE
  #define ADVANCED_PAUSE_PURGE_FEEDRATE        3  // (mm/s) Extrude feedrate (after loading). Should be slower than load feedrate.
  #define ADVANCED_PAUSE_PURGE_LENGTH         50  // (mm) Length to extrude after loading.
  #define ADVANCED_PAUSE_RESUME_PRIME          0  // (mm) Extra distance to prime nozzle after returning from park.
    #define X_CURRENT       800        // (mA) RMS current. Multiply by 1.414 for peak current.
    #define X_CURRENT_HOME  X_CURRENT  // (mA) RMS current for homing. (Typically lower than *_CURRENT.)
    #define X_MICROSTEPS     16        // 0..256
    #define Y_CURRENT       800
    #define Y_CURRENT_HOME  Y_CURRENT
    #define Y_MICROSTEPS     16
    #define Z_CURRENT       800
    #define Z_CURRENT_HOME  Z_CURRENT
    #define Z_MICROSTEPS     16
    #define Z2_CURRENT      Z_CURRENT
    #define Z2_CURRENT_HOME Z_CURRENT_HOME
    #define Z2_MICROSTEPS   Z_MICROSTEPS
    #define E0_CURRENT      800
    #define E0_MICROSTEPS    16
    #define CURRENT_STEP_DOWN     50  // [mA]
    #define REPORT_CURRENT_CHANGE
  #define X_HYBRID_THRESHOLD     100  // [mm/s]
  #define X2_HYBRID_THRESHOLD    100
  #define Y_HYBRID_THRESHOLD     100
  #define Y2_HYBRID_THRESHOLD    100
  #define Z_HYBRID_THRESHOLD       3
  #define Z2_HYBRID_THRESHOLD      3
  #define Z3_HYBRID_THRESHOLD      3
  #define Z4_HYBRID_THRESHOLD      3
  #define I_HYBRID_THRESHOLD       3  // [linear=mm/s, rotational=°/s]
  #define J_HYBRID_THRESHOLD       3  // [linear=mm/s, rotational=°/s]
  #define K_HYBRID_THRESHOLD       3  // [linear=mm/s, rotational=°/s]
  #define U_HYBRID_THRESHOLD       3  // [mm/s]
  #define V_HYBRID_THRESHOLD       3
  #define W_HYBRID_THRESHOLD       3
  #define E0_HYBRID_THRESHOLD     30
  #define E1_HYBRID_THRESHOLD     30
  #define E2_HYBRID_THRESHOLD     30
  #define E3_HYBRID_THRESHOLD     30
  #define E4_HYBRID_THRESHOLD     30
  #define E5_HYBRID_THRESHOLD     30
  #define E6_HYBRID_THRESHOLD     30
  #define E7_HYBRID_THRESHOLD     30
  #define SENSORLESS_HOMING // StallGuard capable drivers only
    #define X_STALL_SENSITIVITY  50
    #define X2_STALL_SENSITIVITY X_STALL_SENSITIVITY
    #define Y_STALL_SENSITIVITY  50
    #define Y2_STALL_SENSITIVITY Y_STALL_SENSITIVITY
    #define Z_STALL_SENSITIVITY  40
    #define Z2_STALL_SENSITIVITY Z_STALL_SENSITIVITY

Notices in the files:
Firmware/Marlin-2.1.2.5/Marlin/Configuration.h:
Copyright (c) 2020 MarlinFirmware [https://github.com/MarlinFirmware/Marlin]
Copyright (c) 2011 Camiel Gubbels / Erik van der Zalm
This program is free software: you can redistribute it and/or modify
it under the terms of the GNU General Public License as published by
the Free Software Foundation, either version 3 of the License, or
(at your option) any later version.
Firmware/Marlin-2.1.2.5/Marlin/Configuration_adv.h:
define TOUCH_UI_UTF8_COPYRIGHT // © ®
